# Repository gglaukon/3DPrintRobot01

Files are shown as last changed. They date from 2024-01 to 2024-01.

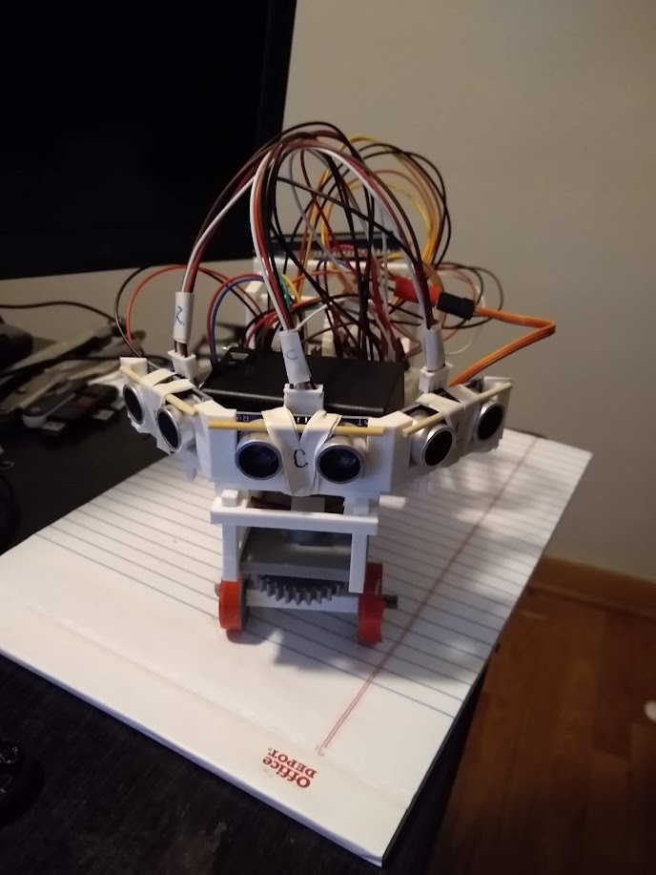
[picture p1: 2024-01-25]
ImagesAndVideos/FrontView.jpg

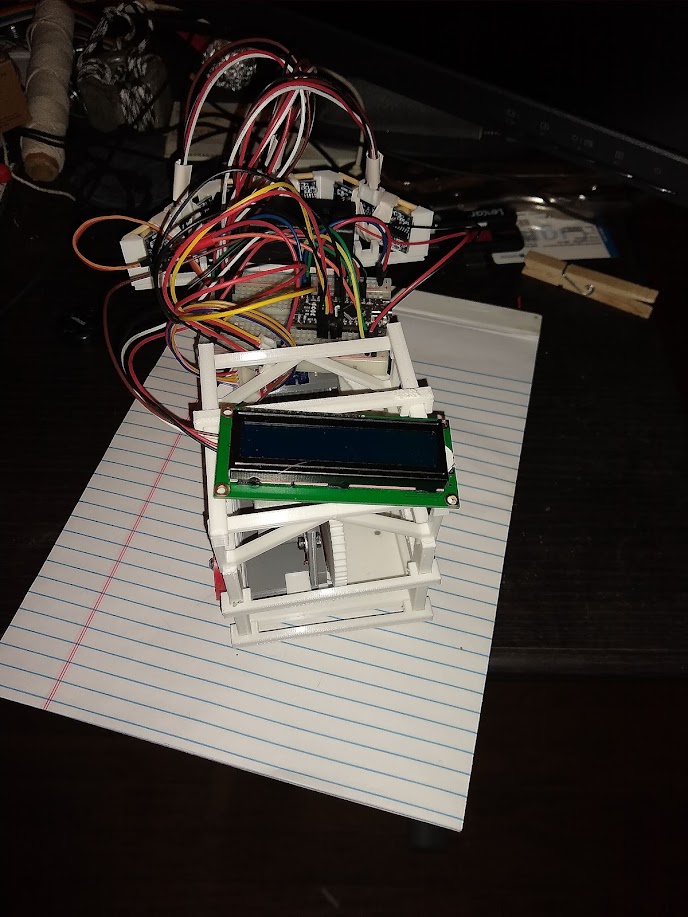
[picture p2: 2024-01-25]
ImagesAndVideos/RearView.jpg

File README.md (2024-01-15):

# 3DPrintRobot01
Initial attempt at a self navigating robot with a 3d printed frame

01 - Overview and Materials
02 - Frame printing notes
03 - Frame Assembly
	A) Drive Plate Assembly
	B) Stearing Plate Assembly
	C) Frame Assembly
04 - Circuit Assembly
05 - Post Assembly Notes

=============================
01 - Overview and Materials
=============================
  This is a design for a simple automated device that is able to path along the ground, avoiding obsticals. The frame is 3D printed, and requires a printing bed of 200mm square minimum. Additionally, the model is composed of...
    - 1 28BYJ-48 stepper motor
    - 1 ULN2003 Stepper motor driver module
    - 1 SG90 servo motor
    - 3 HC-SR04 ultrasonic range finder modules
    - 1 2x16 LCD display
    - 1 LCD1602 I2C module
    - 1 Arduino nano development board
    - 1 30 row breadboard
    - 1 9V battery
    - Glue dots
    - Electrical tape

=============================
02 - Frame printing notes
=============================
	The frame is largely composed of the two motor plates (DrivePlate03 and StearingPlate), and the BodyFrame object. When printing the body frame, print one as-is, and a second one, mirrored lengthwise. Additionally, several BodyClipDriveSide and BodyClipStearingSide objects can be printed and used to stabilize the frame. The ChasisPlatformDriveSide should be printed twice, and then supported further with a few BodyClipDriveSide objects.
	When assembling, parts can be fastened with glue dots, tape, or friction welding.

=============================
03 - Frame Assembly
=============================
	A) Drive Plate Assembly
		PRINT LIST:
		1 x DrivePlate03
		1 x MainDriveGear
		1 x DriveAxelGear
		1 x StepperMount
		2 x DrivePlateAxelMount
		2 x Wheels
		The drive plate is composed of the DrivePlate03, MainDriveGear, DriveAxelGear, DrivePlateAxelMount, StepperMount, and DriveAxel. The stepper motor can be fastened to the StepperMount with adhesive or 3mm screws. Once the motor is fastened, the mount can be slipped between the two prongs on the DrivePlate, and then the MainDriveGear can be attached to the motor spoke. Print two DrivePlateAxelMounts, and attach them to the underside of the platform. Thread the DriveAxel through one of the mounts, fit the DriveAxelGear to interlock with the MainDriveGear through the slot in the middle of the plate, and thread the DriveAxel through the DriveAxelGear and out through the other DrivePlateAxelMount. Print two wheels and fit one to either end of the DriveAxel

	B) Stearing Plate Assembly
		PRINT LIST:
		1 x StearingPlate
		1 x StearingMotorGear
		1 x StearingGear
		1 x StearingColar
		1 x StearingAxelMount
		2 x StearingAxel
		2 x Wheels
		In addition to the printed components, the cross shaped motor fitting should be used in assembly, but not fitted to the motor yet. Adhere the cross fitting to the StearingMotorGear, fit the motor into the rectangular slot on the StearingPlate (so that the motor spoke is closer to the circular hole on the plate), and then screw the StearingAxelGear to the motor. put a StearingColar on the round protrusion of the StearingGear, and then feed the rest of the protrusion through the hole on the StearingPlate. To keep the stearing gear from falling out when the device is picked up, you may want to adhere a piece of raft to the top of the protrusion. feed one axel into the cross shaped hole on the StearingGear, and fit the StearingAxelMount on the other end of the axel. Feed the other StearingAxel through the horizontal opening of the StearingAxelMount, and fit a wheel on either side of the axel

	C) Frame Assembly
		2 x BodyFrame (one nominal, one mirrored)
		1 x SensorHolder
		2 x ChasisPlatformDriveSide
		4+ x BodyClipDriveSide
		4+ x BodyClipStearingSide
		With both motor platforms assembled, take the two BodyFrame and fit them over the plates, so the drive plate is in the rear, and the body frame tapers towards the front, where the stearing plate sits. Use a few of the body clips on the front and back of the frame, and along the top, to stabilize the frame. Take the two ChasisPlatformDriveSide objects, and attach them to the frame, at the furthest extremities of the drive side of the frame (one at the furthest edge of the rear, and one as close to the taper as possible), and use a few BodyClipDriveSide objects to support it. Adhere a BodyClipStearingSide to the front of the SensorHolder, and then tape a few BodyClipDriveSide together, so that it makes solid contact with both far ends of the Sensor holder, giving support to the rear of the sensor holder when it is fitted to the front of the frame. With the sensor holder assmebled, fit the sensors into the slots of the holder

=============================
04 - Circuit Assembly
=============================
	On the breadboard, attach the positive terminal of the 9V battery to one of the power rails on the breadboard, and the negative terminal to one of the ground rails. Plug the arduino into the center of the breadboard, so the USB port is at the edge (for ease of reference, it will be assumed that the controller is plugged in to the row 30 side of the breadboard). Connect the 5V pin of the arduino to the other power rail on the breadboard, and connect the ground pin on the arduino to one of the ground rails on the breadboard, and install a jumper wire accross the two ground rails. Connect the 9V rail to the Vin pin of the arduino. 
	Connect the data pins for the right, center, and left sensors to the A0, A1, and A2 pins respectively and the power pins to the 5V rail (ground can be tied to either ground rail). Connect the signal wire for the servo to pin 9, and the power pin to the 9V rail. Connect the motor driver pins 1, 2, 3, and 4 to arduino pins 5, 4, 3, and 2 respectively, and the power pin to the 9V rail. For the LDC screen, connect the SDA pint to A1, and the SDC to A0, and the power pin to the 5V rail

=============================
05 - Post Assembly Notes
=============================
	Once the assembly is complete, plug the arduino into your PC, and upload the controll script. It is advised that you disconnect the motors for this process. Once the script is uploaded to the arduino, you should be able to disconnect it from the PC (Reconnect the motors) and it should run when you turn the 9V rail on. The turning apparatus, however, may need some fine tuning, based on how it was installed. The lines of code that dictate the angles the servo turns to for center, right, and left turns are on 160, 161, and 164 respectively

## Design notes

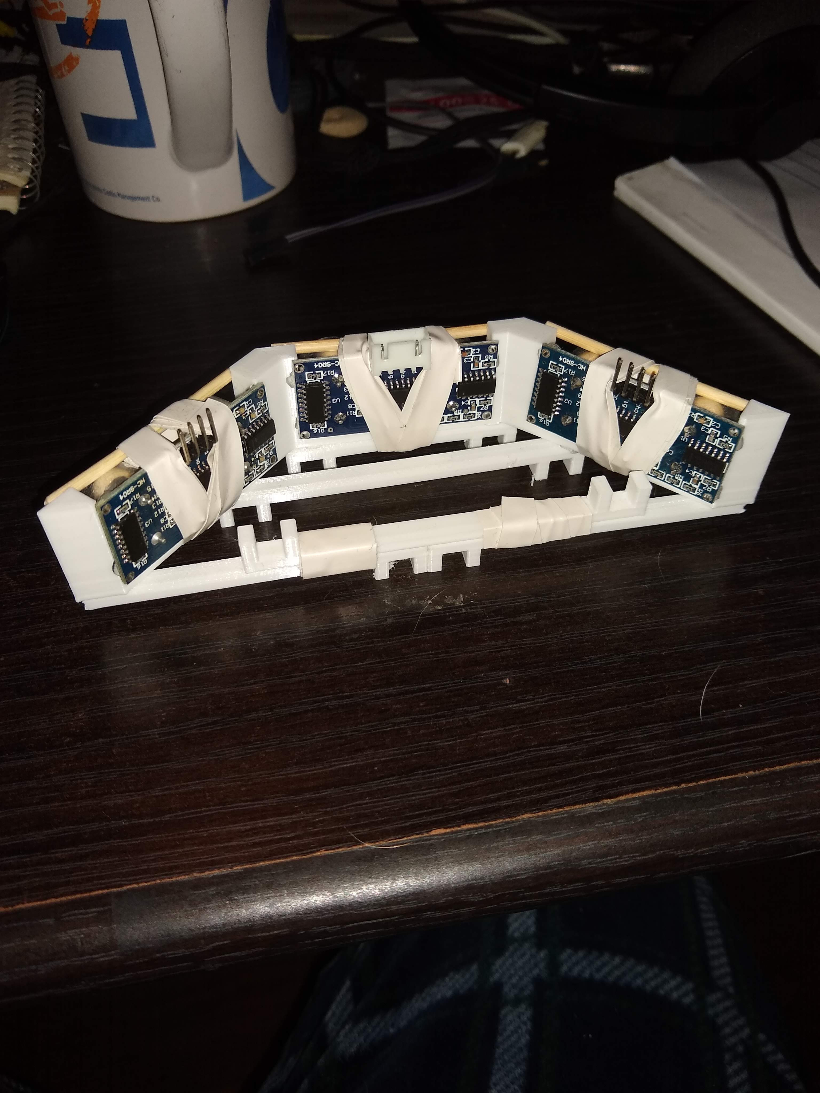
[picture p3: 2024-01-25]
ImagesAndVideos/SensorHolder/Sensor Rear.jpg

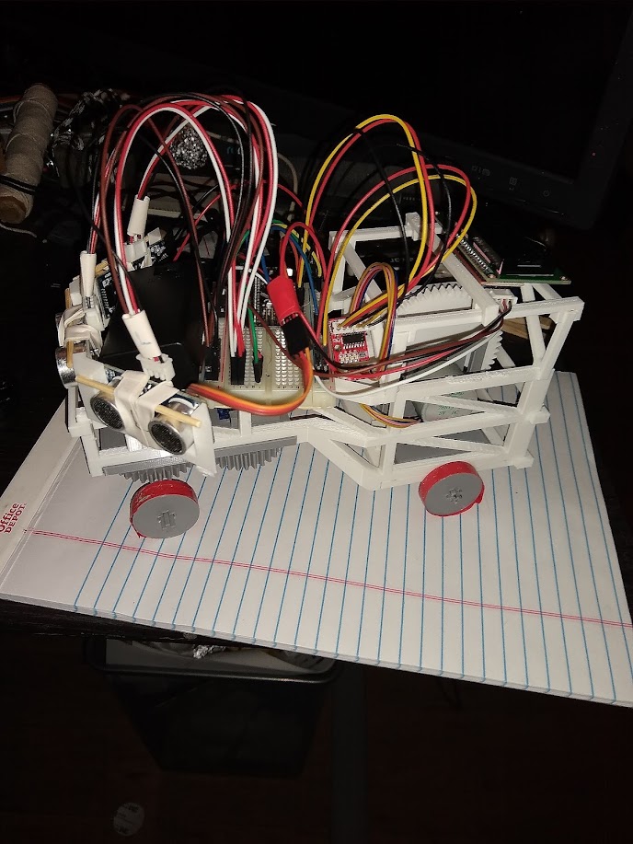
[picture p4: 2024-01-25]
ImagesAndVideos/LeftSideView.jpg

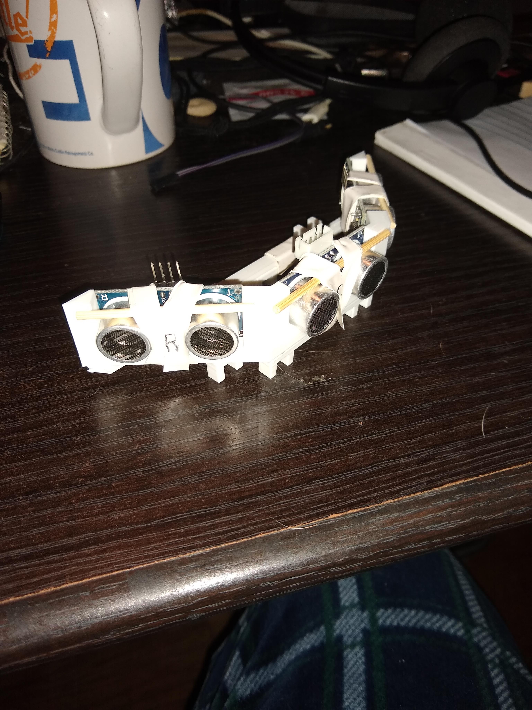
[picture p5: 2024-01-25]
ImagesAndVideos/SensorHolder/SensorRightSide.jpg

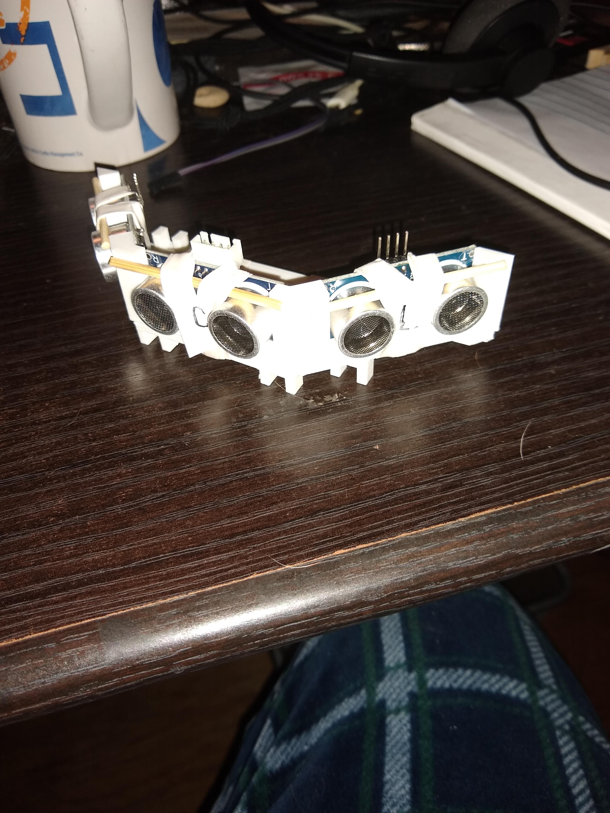
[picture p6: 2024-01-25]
ImagesAndVideos/SensorHolder/Sensor Left Side.jpg

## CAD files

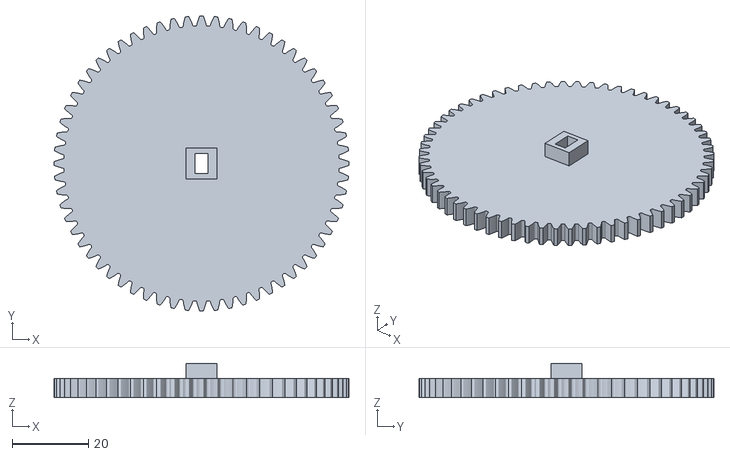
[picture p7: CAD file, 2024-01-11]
Parts/DriveApparatus/MainDriveGear.stl
77.2 x 77.2 x 9.00

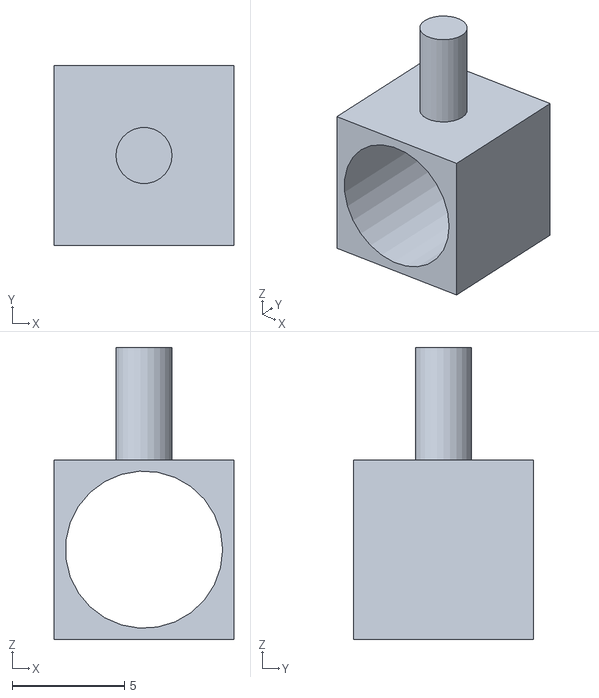
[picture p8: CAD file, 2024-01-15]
Parts/DriveApparatus/DrivePlateAxelMount.stl
8.00 x 8.00 x 13.0

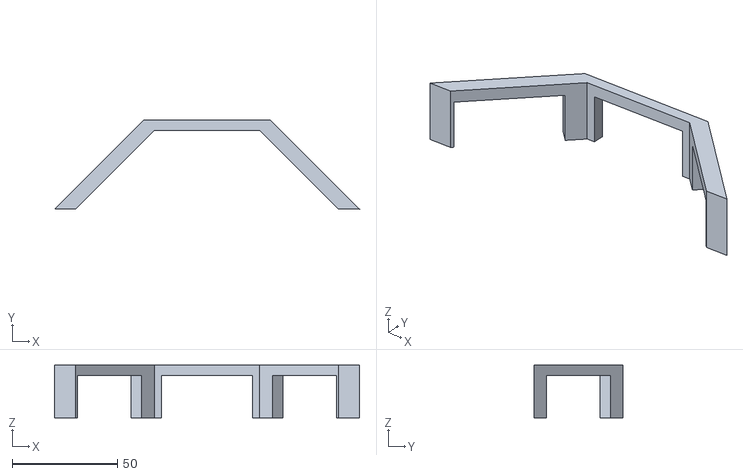
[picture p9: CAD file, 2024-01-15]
Parts/FrameParts/SensorHolder.stl
144.9 x 42.4 x 25.0

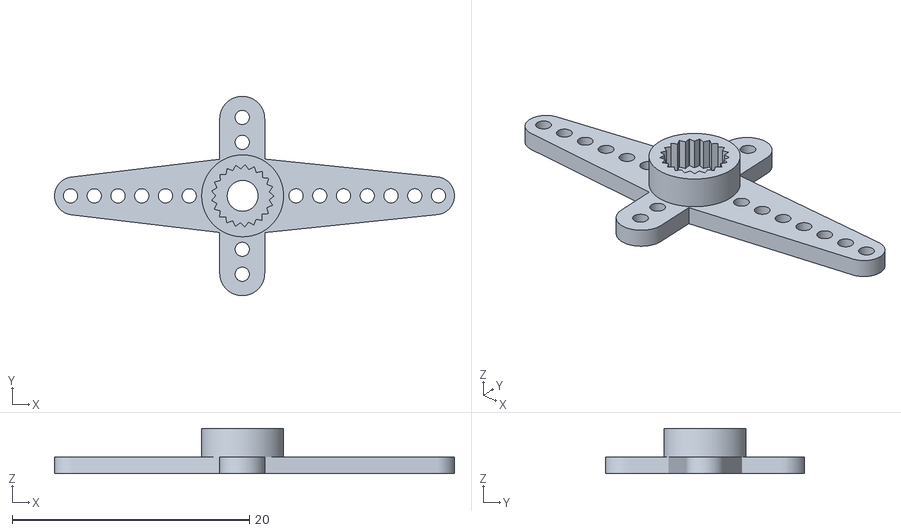
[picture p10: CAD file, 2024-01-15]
Parts/StearingApparatus/SG90_Servo_Horn-5.stl
33.7 x 16.8 x 3.82

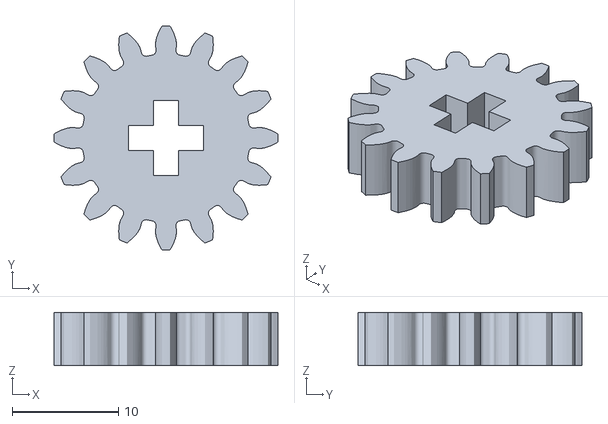
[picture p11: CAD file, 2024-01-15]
Parts/DriveApparatus/DriveAxelGear.stl
21.1 x 21.1 x 5.00

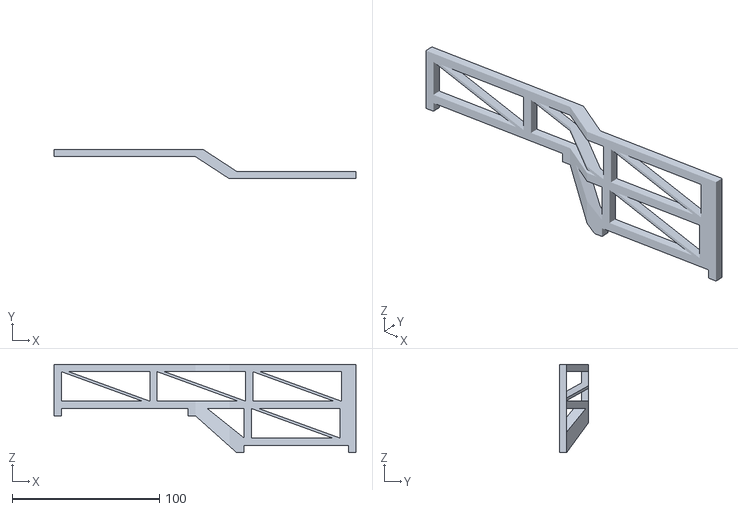
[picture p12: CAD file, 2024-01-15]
Parts/FrameParts/BodyFrame.stl
205.0 x 20.0 x 60.0

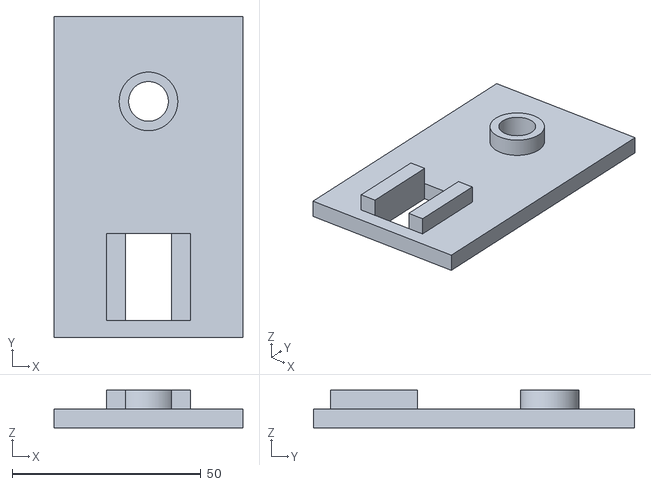
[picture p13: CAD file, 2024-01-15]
Parts/StearingApparatus/StearingPlate.stl
50.0 x 85.0 x 10.0

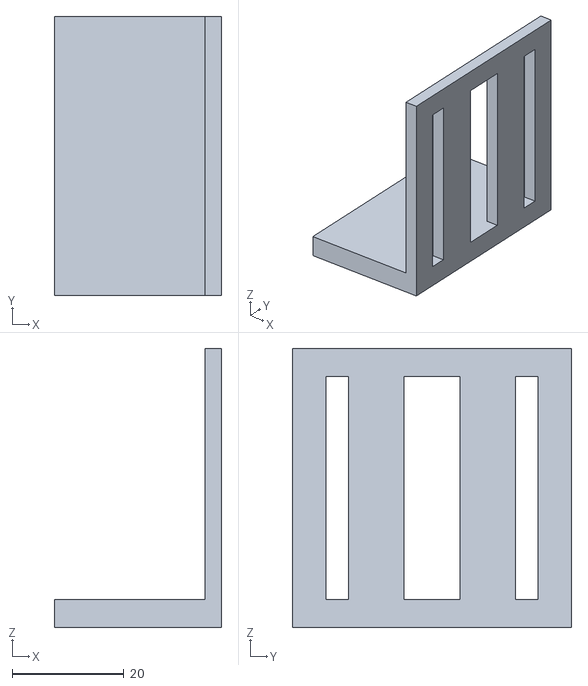
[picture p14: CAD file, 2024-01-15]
Parts/DriveApparatus/StepperMount.stl
30.0 x 50.0 x 50.0

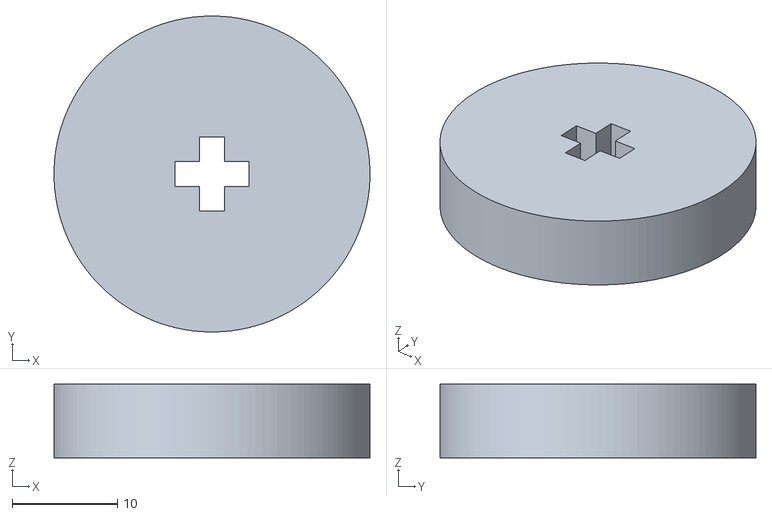
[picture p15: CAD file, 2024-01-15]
Parts/FrameParts/Wheel.stl
30.0 x 30.0 x 7.00

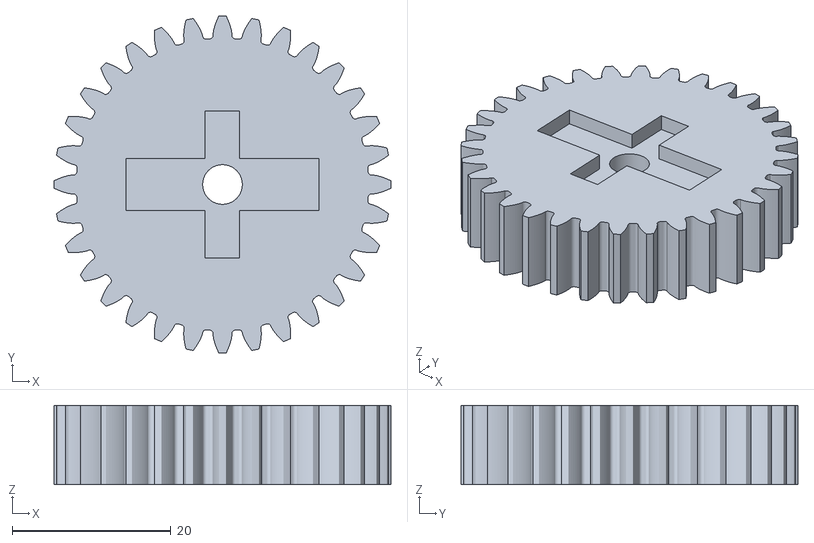
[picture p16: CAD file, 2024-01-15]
Parts/StearingApparatus/StearingMotorGear.stl
42.5 x 42.5 x 10.0

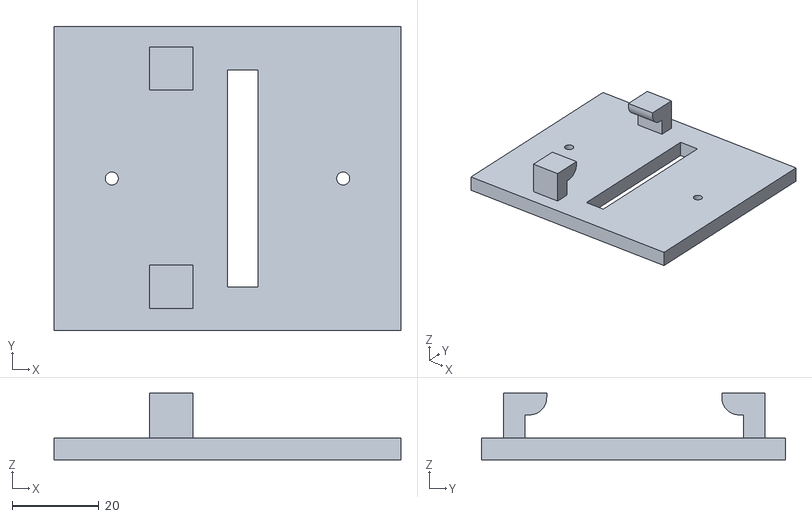
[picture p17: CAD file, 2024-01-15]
Parts/DriveApparatus/DrivePlate03.stl
80.0 x 70.0 x 15.4

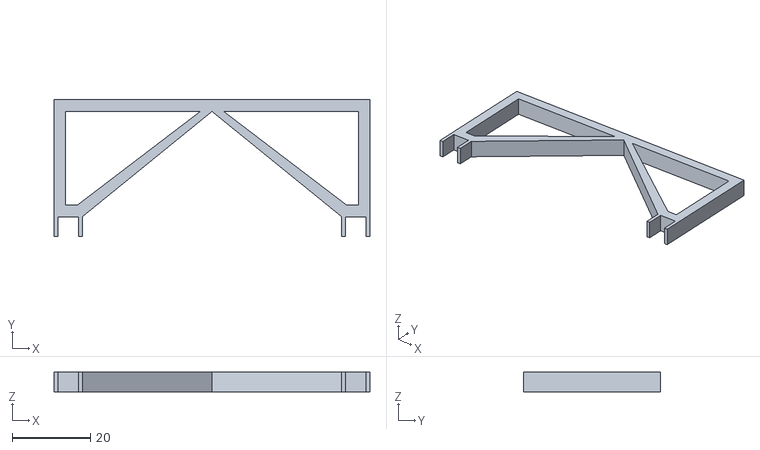
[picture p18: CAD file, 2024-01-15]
Parts/FrameParts/ChasisPlatformDriveSide.stl
81.0 x 35.0 x 5.00

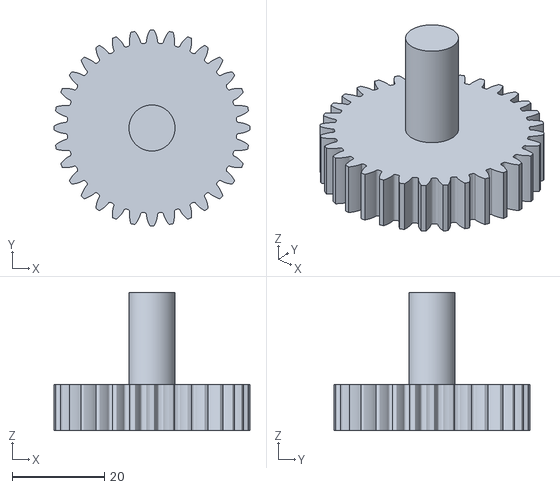
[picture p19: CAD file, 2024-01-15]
Parts/StearingApparatus/StearingGear.stl
42.5 x 42.5 x 30.0

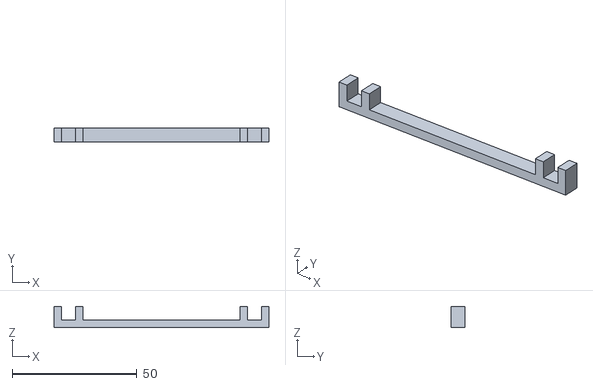
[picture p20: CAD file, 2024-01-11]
Parts/FrameParts/BodyClipDriveSide.stl
86.0 x 5.50 x 8.50

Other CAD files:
Parts/StearingApparatus/StearingAxelMount.stl
Parts/DriveApparatus/DriveAxel.stl
Parts/FrameParts/BodyClipStearingSide.stl
Parts/StearingApparatus/StearingAxel.stl
Parts/StearingApparatus/StearingColar.stl

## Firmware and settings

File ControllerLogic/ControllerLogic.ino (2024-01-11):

#include <Stepper.h>
#include <Servo.h>
#include <Wire.h>
#include <LiquidCrystal_I2C.h>





// ==============================================
// ---------- Start Sensor Functions ------------
//===============================================
// == == the sensor_update() function is the main tool in this section
// == == The sensor_update() function 
// == Sensor References
int sensor_right = A0;
int sensor_cent = A1;
int sensor_left = A2;


// == sensor array designations
const int sensor_samp_size = 6;   // -- The number of samples to base distance calculation off of
const int sensor_array_size = sensor_samp_size + 1; // - the total size of the array, including average value at the end
// == == Extra sensor array columns
const int sensor_adj_loc = sensor_array_size - 1; // - the index of the adjusted value in the array
    // -- adjusted value is the value remaining after the noise (errant highs/lows) has been cut out
//const int sensor_prnt_loc = sensor_array_size - 1;

long sensor_right_dists[sensor_array_size];
long sensor_cent_dists[sensor_array_size];
long sensor_left_dists[sensor_array_size];

void array_queue(long in_array[sensor_array_size], long value){
  // == Allows the provided array to behave like a queue, (FIFO)
  for(int x = sensor_samp_size - 1; x >= 1; x--){
    in_array[x] = in_array[x - 1];
  }
  in_array[0] = value;
}

void bubble_sort(long in_array[sensor_samp_size]){
  // -- -- -- -- 1) Create a flag for whether a swap has been made
  // -- -- -- -- 2) itterate through the array elements
  // -- -- -- -- -- 2a) if the next element of the array is less than the current element, swap
  // -- -- -- -- -- 2b) set flag to show a swap was made
  // -- -- -- -- -- 2c) return to step 2a, untill the last element has been reached
  // -- -- -- -- 3) if the swap flag has been triggered, reset flag and restart at step 2
  // -- -- -- -- -- if the flag has not been triggered, elements are sorted
  bool swap = 0;
  for (int sort_ind = 0; sort_ind < (sensor_samp_size - 1); sort_ind++){
    if(in_array[sort_ind] > in_array[sort_ind + 1]){
      long buffer = in_array[sort_ind + 1];
      in_array[sort_ind + 1] = in_array[sort_ind];
      in_array[sort_ind] = buffer;
      swap = 1;
    }
}
  if(swap == 1){
    bubble_sort(in_array);
  }
}

void array_median(long in_array[sensor_array_size]){
  // == updates the last element of the provided array (in_array) to be the median of 
  // == == the preceeding elements, via bubble sort (bubble_sort())

  // == 1) sort the sort array
  long sort_array[sensor_samp_size];              // -- create the sort array
  for(int x = 0; x < sensor_samp_size; x++){      // -- load the sort array
    sort_array[x] = in_array[x];}                 // -- load 1:1
  bubble_sort(sort_array);

  // == 2) Determine the Median value
  long median;
  if(sensor_samp_size % 2 == 0){
    // -- -- -- if sample size is even, take average of middle two values
    median = (sort_array[sensor_array_size / 2] + sort_array[(sensor_array_size / 2) - 1]) / 2;
  }
  if(sensor_samp_size % 2 == 1){
    // -- -- -- if the sample size is odd, take middle value
    median = sort_array[(sensor_array_size - 1) / 2];
  }

  // == 3) Update sample array with median value
  in_array[sensor_adj_loc] = median;
}

long range_find(int sensor_pin){
  // == send a square wave to a sensor (sensor_pin), return the resulting distance in cm (cm_dist)
  pinMode(sensor_pin, OUTPUT);
  digitalWrite(sensor_pin, LOW);
  delayMicroseconds(2);
  digitalWrite(sensor_pin, HIGH);
  delayMicroseconds(10);
  digitalWrite(sensor_pin, LOW);

  // == get the response time from the sensor, convert to cm
  pinMode(sensor_pin, INPUT);
  long raw_dist = pulseIn(sensor_pin, HIGH);
  long cm_dist = raw_dist / (29 * 2);
  if (cm_dist > 30){
    cm_dist = 30;
  }
  return cm_dist;
}

void print_array(long in_array[sensor_array_size], String pref){
  // == used for debugging purposes, prints out each value of a given array (in_array)
  // == == with a provided preface (perf)
  Serial.println(" ");
  Serial.print(pref);
  Serial.print(": ");
  for (int x = 0; x < sensor_array_size; x++){
    if(x != 0){
      Serial.print(", ");
    }
    Serial.print(in_array[x]);
  }
}


void sensor_update(int sensor, long in_array){
  // == read the distance of a given sensor (sensor, range_find()), and add the value
  // == == to the provided array (in_array), via queue operation (array_queue()) to retain chronology.
  // == == update current median value of the array (array_median())
  long dist_read = range_find(sensor);
  array_queue(in_array, dist_read);
  array_median(in_array);
}

void sensor_check(){
  // == Calls sensor_update() function on all sensors, which adds a new value
  // == == sensor sample to the sensor array, and updates the median value
  int sensor_ping_delay = 50;
  sensor_update(sensor_right, sensor_right_dists);
  delay(sensor_ping_delay);
  sensor_update(sensor_cent, sensor_cent_dists);
  delay(sensor_ping_delay);
  sensor_update(sensor_left, sensor_left_dists);
  delay(sensor_ping_delay);

  print_array(sensor_right_dists, "Right: ");
  print_array(sensor_cent_dists, "Center: ");
  print_array(sensor_left_dists, "Left: ");
}

// ==============================================
// XXXXXXXXXX End Sensor Functions XXXXXXXXXXXXXX
//===============================================

// ==============================================
// ----------- Start Servo Functions ------------
//===============================================

// == Servo References
int pwm_delay = 50;
int servo_pin = 9;
Servo turn_servo;

int turn_deg_center = 55;
int turn_deg_right = 30;
//** updated again from 35 to 30
//** updated from 40 to 35 (initial version)
int turn_deg_left = 90;
//** updated again from 85 to 90
//** updated from 80 to 85(initial version)
int turn_previous = turn_deg_right;    // for reverse turning
int turn_direction = 0; // indicates the current direction of the stearing motor
  // -1 = left, 0 = center, 1 = right

void turn_stearing(int dir){
  // -- Set motor direction
  for (int inc = 0; inc <= 10; inc++){
    turn_servo.write(dir);
  }
  // -- Update prev_tur flag
  if (dir == turn_deg_left){
    turn_previous = -1;
  }
  if (dir == turn_deg_right){
    turn_previous = 1;
  }
}

// ==============================================
// XXXXXXXXXXXX End Servo Functions XXXXXXXXXXXXX
//===============================================

// ==============================================
// --------- Start Stepper Functions ------------
//===============================================
// == Stepper References
int total_steps = 200;
int step_inc = 200;
int step_speed = 60;
int prev_drive_dir = 0;        
Stepper stepper(total_steps, 5, 3, 4, 2); // middle pins need to be flipped to function correctly
int drive_forward = -1;
int drive_reverse = 1;
int rev_adj = 6; // the reverse operations require more drive time, to clear obsticals
int drive_direction = drive_forward; // indicates the current direction of motion
  // 1 = Backwards, 0 = stopped, -1 = forward

void stepper_drive(int dir){
  stepper.step(step_inc * dir);
}
// ==============================================
// XXXXXXXXXXX End Stepper Functions XXXXXXXXXXXX
//===============================================

// ==============================================
// ----------- Start LCD Functions --------------
//===============================================
//char top_line[16] = "L=X | C=X | R=X ";    // - spots at 2, 8, and 14

LiquidCrystal_I2C lcd(0x27, 2, 1, 0, 4, 5, 6, 7, 3, POSITIVE);
// -- http://www.handsontec.com/dataspecs/module/I2C_1602_LCD.pdf
// -- -- Create the lcd i2c reference, useing
// -- -- adr = burnt in address
// -- -- en, rw, rs = just as they are on the board
// -- -- d1, d4, d5, d6, d7 = the D0-D5 pins



void update_screen(char new_l, char new_c, char new_r, char new_d, char new_s){
  char top_line[16] = "L=X | C=X | R=X ";    // - spots at 2, 8, and 14
  char bottom_line[16] = "   X   |    X   ";   // - open spots at 4 and 13
  // -- clear the screen
  lcd.clear();

  // -- print the top row
  top_line[2] = new_l;
  top_line[8] = new_c;
  top_line[14] = new_r;
  lcd.setCursor(0, 0);
  lcd.print(top_line);

   // -- print bottom row
  bottom_line[3] = new_d;
  bottom_line[12] = new_s;
  lcd.setCursor(0, 1);
  lcd.print(bottom_line);
}


// ==============================================
// ------------ End LCD Functions ---------------
//===============================================


// ==============================================
// ---------- Begin Logic Functions -------------
//===============================================

void sense_logic(){
  int close_flag_dist = 15;
  //** Updated from 10 (Initial version)
  int flag_count = 0;
  char l_char = 'N';
  char c_char = 'N';
  char r_char = 'N';
  char d_char = 'F';
  char s_char = 'C';

  // for each sensor who's read is LT-EQ to teh flag distance, adjust the flag_count
  // -- flag count is not a linear count, but an encoding
  // -- left = 1, center = 2, right = 4
  if (sensor_left_dists[sensor_adj_loc] <= close_flag_dist) {
    flag_count = flag_count + 1;
    l_char = '!';
  }
  if (sensor_cent_dists[sensor_adj_loc] <= close_flag_dist) {
    flag_count = flag_count + 2;
    c_char = '!';
  }
  if (sensor_right_dists[sensor_adj_loc] <= close_flag_dist) {
    flag_count = flag_count + 4;
    r_char = '!';
  }
  Serial.println(" ");
  Serial.println(flag_count);
  switch(flag_count){
    case 0:
      // no triggers
      // -- -- Set comm values
      // - turn Center
      s_char = 'C';
      // - drive forward
      d_char = 'F';

      // -- -- orders
      turn_stearing(turn_deg_center);
      stepper_drive(drive_forward);

      break;

    case 1:
      // left triggered
      // -- -- Set comm values
      // -- turn right
      s_char = 'R';
      // -- drive forward
      d_char = 'F';

      // -- -- orders
      turn_stearing(turn_deg_right);
      turn_previous = turn_deg_right;
      stepper_drive(drive_forward);
      break;

    case 2:
      // center triggered
      // -- -- Set comm values
      // -- turn same direction as previous turn
      int rev_dir;
      if (turn_previous == turn_deg_left) {
        // turn left
        s_char = 'L';
        rev_dir = turn_deg_left;
      }
      if (turn_previous == turn_deg_right) {
        // turn right
        s_char = 'R';
        rev_dir = turn_deg_right;
      }
      // -- drive reverse
      d_char = 'R';

      // -- -- orders
      turn_stearing(rev_dir);
      stepper_drive(drive_reverse * rev_adj);
      break;

    case 3:
      // left and center triggered
      // -- -- Set comm values
      // -- turn left
      s_char = 'L';
      // -- drive reverse
      d_char = 'R';

      // -- -- orders
      turn_stearing(turn_deg_left);
      stepper_drive(drive_reverse * rev_adj);
      break;

    case 4:
      // right triggered
      // -- -- Set comm values
      // -- turn left
      s_char = 'L';
      // -- drive forward
      d_char = 'F';

      // -- -- orders
      turn_stearing(turn_deg_left);
      stepper_drive(drive_forward);
      break;

    case 5:
      // left and right triggered
      // -- -- Set comm values
      // -- turn center
      s_char = 'C';
      // -- drive forward
      d_char = 'F';

      // -- -- orders
      turn_stearing(turn_deg_center);
      stepper_drive(drive_forward);
      break;

    case 6:
      // center and right triggered
      // -- -- Set comm values
      // -- turn right
      s_char = 'R';
      // -- drive reverse
      d_char = 'R';

      // -- -- orders
      turn_stearing(turn_deg_center);
      stepper_drive(drive_forward);
      break;

    case 7:
      char s_char_1;
      char s_char_2;
      int tpt_for;
      int tpt_rev;
      if (turn_previous == turn_deg_right) {
        tpt_rev = turn_deg_right;
        tpt_for = turn_deg_left;
        s_char_1 = 'R';
        s_char_2 = 'L';
      }
      if (turn_previous == turn_deg_left) {
        tpt_rev = turn_deg_left;
        tpt_for = turn_deg_right;
        s_char_1 = 'L';
        s_char_2 = 'R';
      }

      s_char = s_char_1;
      d_char = 'R';
      turn_stearing(tpt_rev);
      stepper_drive(drive_reverse * rev_adj);

      break;
    default:
      // should not happen
      break;
  }
  update_screen(l_char, c_char, r_char, d_char, s_char);
}

// ==============================================
// ----------- End Logic Functions --------------
//===============================================


void setup() {
  Serial.begin(9600);
  stepper.setSpeed(step_speed);
  turn_servo.attach(servo_pin);
  lcd.begin(16, 2);
  lcd.backlight();
}

void logic_loop(){
  // -- populate sensor arrays with current information
  for (int pop_x = 0; pop_x < sensor_samp_size; pop_x++){
    sensor_check();
  }

  // -- run loop for a certain number of times
  //for (int loop_x = 0; loop_x < 5; loop_x++){
  while (true){
    for (int check_x = 0; check_x < ((sensor_samp_size / 2) + 1); check_x++){
      sensor_check();
    }
    sense_logic();
  }
  
}

void loop() {
  int rout_delay = 1000;
  Serial.println("----------Process Starting---------");
  logic_loop();
  //sensor_debug();
  //motor_debug();
  // -- 1) Check surroundings
  //sensor_check();

  // -- 2) Adjust servo accordingly

  // -- 3) Engage Stepper forward/backward

  // -- update user
  //update_screen();
  delay(rout_delay);
}

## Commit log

2024-01-11 Added Logic Script
    Added folder with arduino script for control and navigation
2024-01-11 Added folder for 3D printed parts
    Added folder with the FreeCAD project file, along with final part STLs
2024-01-11 Added individual STL files for parts
    [2023.07.19-FullCad-Wheels.stl, Axel.stl, BodyClipDriveSide.stl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]
2024-01-15 Delete Parts directory
    Deleted old Parts file, to make room for new, better organized version
    [2023.07.19-FullCad-Wheels.stl, Axel.stl, BodyClipDriveSide.stl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]
2024-01-15 Update README.md
    Updated README to include instructions for assembly
2024-01-15 Added better organized Parts folder
    [BodyClipDriveSide.stl, BodyClipStearingSide.stl, BodyFrame.stl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]
2024-01-15 Added Servo Horn file
    [SG90_Servo_Horn-5.stl]
2024-01-15 Update README.md
    Updated readme to include post-assembly guidance
